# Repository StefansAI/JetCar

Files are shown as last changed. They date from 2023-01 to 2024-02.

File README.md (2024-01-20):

<h1 style="text-align: center;">JetCar</h1>
<h2 style="text-align: center;">The mini self-driving car project</h2>
<br>
<div style="text-align: center;">
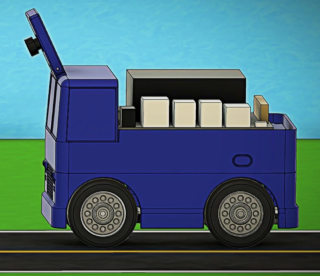
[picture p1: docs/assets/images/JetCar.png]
  
</div>
<br>
The JetCar project is based on ideas from <a href="https://github.com/NVIDIA-AI-IOT/jetbot">JetBot</a> and <a href="https://github.com/NVIDIA-AI-IOT/jetracer">JetRacer</a>. It utilizes the <a href="https://developer.nvidia.com/embedded/jetson-nano-developer-kit">Jetson Nano Developer Kit</a>, the OLED display and battery pack from JetBot and the steering servo control from JetRacer. But this project includes a completely new mechanical design, as compact as possible with these components. 
The goal is not speed or road following alone, but navigating on a street map autonomously, recognizing intersections and turning left or right on user request when the turn is allowed. To do this, JetCar has to recognize intersections and a few signs on the street.
<br>
<div style="text-align: center;">
  
</div>
<br>
The project is organized into following folders:
<br><br>

1. firmware
    - jetcar: Jupyter notebooks and python files to run in the JetCar
    - offline_debug: python files for offline debugging of firmware recordings
    - SD card install script 
<br><br>

2. mechanical
    - step_files: all step files of the car design
    - stl_files: all stl files for 3D printer
<br><br>

3. tools
    - bin: Windows executables
    - source: Full C# source code projects for the executables 
    - Jupyter notebook for training
<br><br>

To download just one sub folder from this repository, <a href="https://www.gitkraken.com/learn/git/github-download#how-to-download-a-folder-from-github">read here</a> or enter the URL directly in <a href="https://download-directory.github.io/"> https://download-directory.github.io/.</a> 
<br><br>
More documentation:<br>
- <a href="docs/BOM.md">BOM</a><br>
- <a href="docs/Assembly.md">Assembly</a><br>
- <a href="docs/SD%20Card%20Setup.md">SD Card Setup</a><br>
- <a href="docs/Data%20Preparation.md">Data Preparation with ImageSegmenter</a><br>
- <a href="docs/Model%20Training.md">Model Training</a><br>
- <a href="docs/StreetMaker.md">Street Maker</a><br>
- <a href="docs/Operation.md">Operation</a><br>
- <a href="docs/Debugging.md">Debugging</a><br>
<br><br>
Videos:<br>
- <a href="https://youtu.be/Dyagu1U4WaQ">JetCar Part 1 - Introduction</a><br>
- <a href="https://youtu.be/SRJtpAVrnXM">JetCar Part 2 – Assembly</a><br> 
- <a href="https://youtu.be/EU15R7dB3os">JetCar Part 3 - Firmware Setup</a><br>
- <a href="https://youtu.be/G4PKwO-Vvck">JetCar Part 4 - Data Preparation</a><br>
- <a href="https://youtu.be/1_ItpaHLQUw">JetCar Part 5 - Model Training</a><br>
- <a href="https://youtu.be/k-taHFnwKoY">JetCar Part 6 - StreetMaker</a><br>
- <a href="https://youtu.be/uBuOR0Mm2eY">JetCar Part 7 - Firmware</a><br>
- <a href="https://youtu.be/s89fhRwG_2A">JetCar Part 8 - Demonstration</a><br>
<br><br>

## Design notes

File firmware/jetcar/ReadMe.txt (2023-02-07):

Copy the contents of notebooks into the $HOME/JetCar/notebooks folder of the Jetson Nano via Jupyter.

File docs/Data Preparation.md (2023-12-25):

<h1 style="text-align: center;">JetCar</h1>
<h2 style="text-align: center;">Data Preparation with ImageSegmenter</h2>
<br><br>
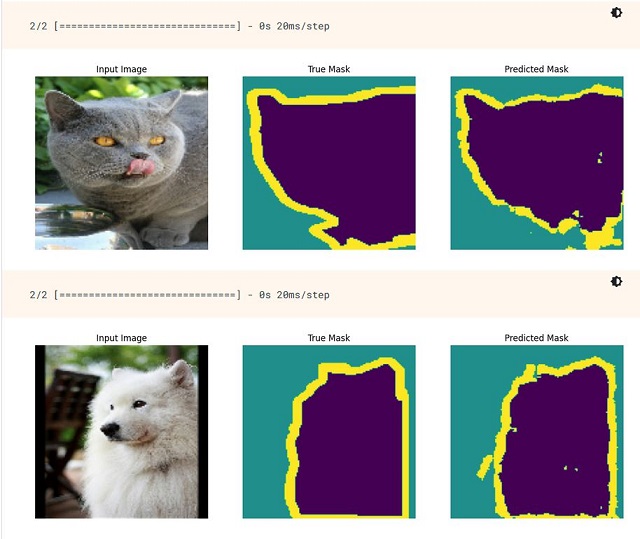
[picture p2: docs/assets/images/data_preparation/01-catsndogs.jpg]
<br><br>
Tensorflow.org has very nice <a href="https://www.tensorflow.org/tutorials/images/segmentation">tutorials to go through and even execute online.</a> One of them is about <a href="https://www.tensorflow.org/tutorials/images/segmentation">Image Segmentation</a> and the example is using a cats and dogs dataset. The model is trained on a mask to separate background from animal.
<br><br>
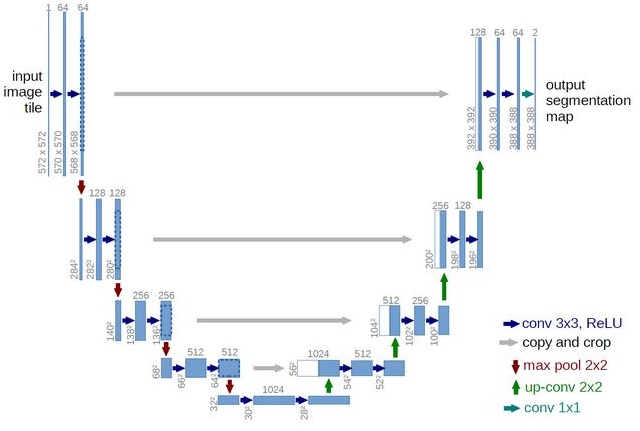
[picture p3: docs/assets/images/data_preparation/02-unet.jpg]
<br><br>
The <a href="https://lmb.informatik.uni-freiburg.de/people/ronneber/u-net/">U-Net</a> architecture contains a downsample path followed by an upsample path, abstracting features and resulting in a classification map. 
<br><br>
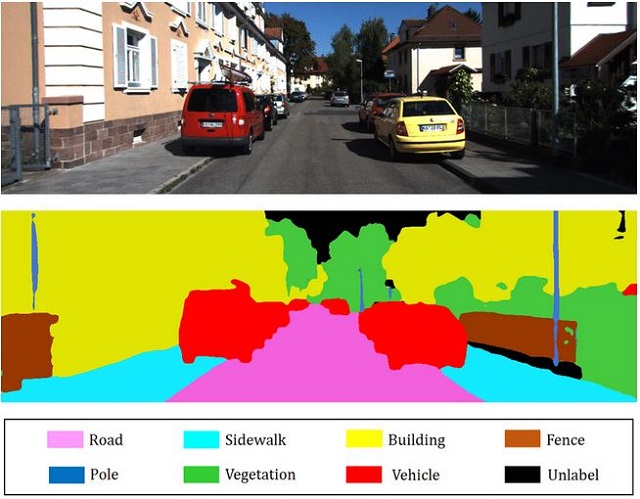
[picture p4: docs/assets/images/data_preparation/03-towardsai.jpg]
<br><br>
There are a lot of examples online. This one from the <a href="https://towardsai.net/p/l/machine-learning-7">TowardsAI Website</a> looks like something for this project.
<br><br>
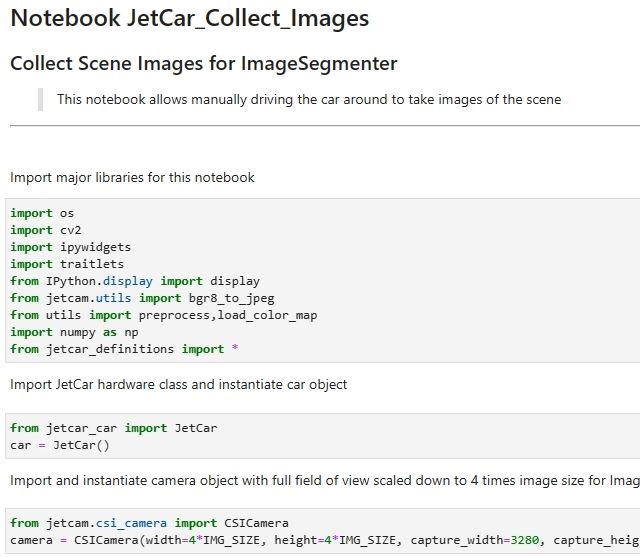
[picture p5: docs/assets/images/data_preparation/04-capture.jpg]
<br><br>
The <a href="https://github.com/NVIDIA-AI-IOT/jetbot">JetBot</a> project contained a Jupyter notebook to capture images of the scene for its own training (data_collection.ipynb). A similar version is part of the firmware notebooks for the JetCar (<a href="https://github.com/StefansAI/JetCar/tree/main/firmware/jetcar/notebooks/JetCar_Collect_Images.ipynb">JetCar_Collect_Images.ipynb</a>).<br>It allows manually driving the car around remotely and to hit a button to capture scene images. When done, the recorded images can be zipped and downloaded to the PC.<br>
JetBot and JetCar use image sizes of 224x224 for the inference. For better data augmentation however, the recorded images are here 4 times as big in both dimensions. 
<br><br>
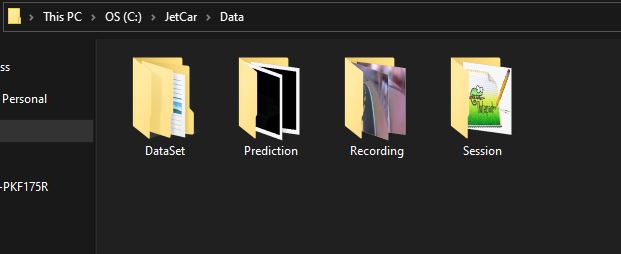
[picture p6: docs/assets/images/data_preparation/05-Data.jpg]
<br><br>
Now a tool was needed to create masks for each image. This tool happens to be now part of this repository as <a href="https://github.com/StefansAI/JetCar/tree/main/tools/bin/ImageSegmenter">compiled executable </a>and as <a href="https://github.com/StefansAI/JetCar/tree/main/tools/source/ImageSegmenter">full source code project.</a><br>
The Data folder for the ImageSegementer has to have a subfolder called "Recording", where all captured images need to go. 
<br><br>
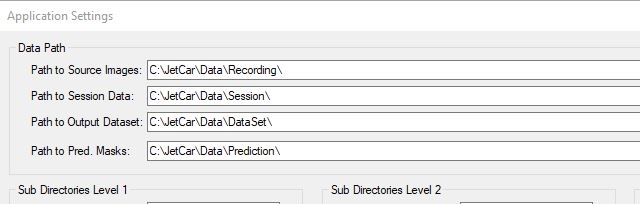
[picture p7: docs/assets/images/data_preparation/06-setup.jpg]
<br><br>
The very first time, this application is executed, it might prompt you to check and possibly correct the data path entries in the Settings dialog. A configuration file will be created to reload the last settings at startup.
<br><br>
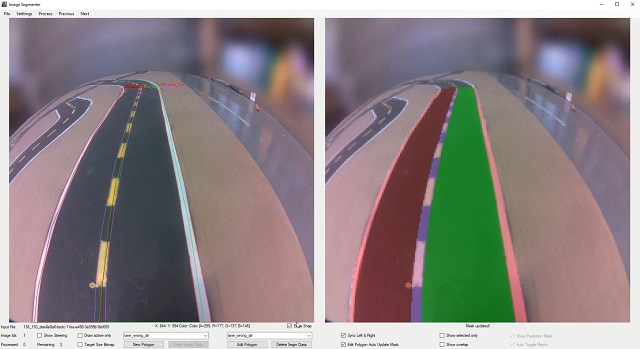
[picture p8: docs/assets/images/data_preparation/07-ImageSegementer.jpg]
<br><br>
The basic idea of this application is going through the recorded images one by one and creating the mask for each. The full resolution image is shown on the left side and the downsampled version as background on the right.
<br><br>
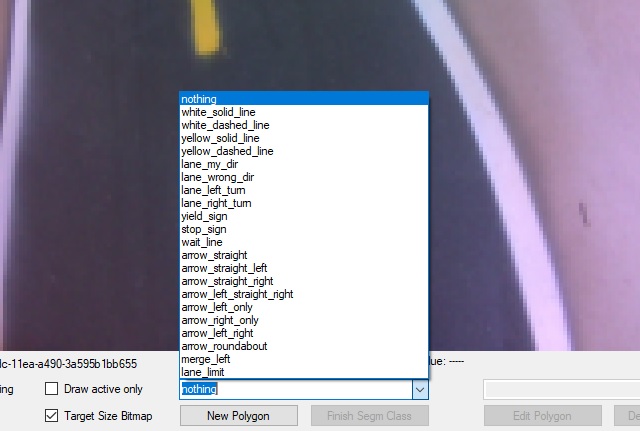
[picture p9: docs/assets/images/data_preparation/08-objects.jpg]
<br><br>
Every area to represent any specific class will have to be outlined with a polygon. To start outlining, select an object class from the combo box and hit "New Polygon". <br>Outline the area with the mouse and left click everywhere, where a polygon point needs to be added. When close to an edge, the point will be automatically snapped to the edge, but this function can be disabled with a check box. <br>A left double click closes the polygon and ends the mouse entry. Hit the "Finish Segm Class" button to finalize it. The polygon changes to the class color and the enclosed area appears in the same color transparent on top of the scene background on the right side.
<br><br>
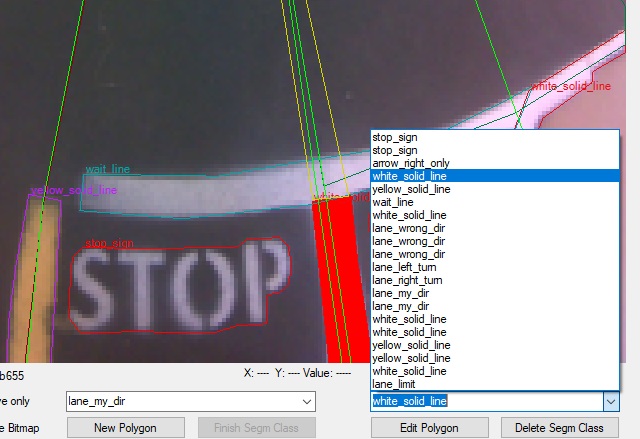
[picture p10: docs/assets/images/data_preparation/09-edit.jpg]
<br><br>
Every class polygon already entered will show up in the edit combobox. To identify the correct one out of several same classes, click on one and it will be highlighted as red filled polygon.
<br><br>
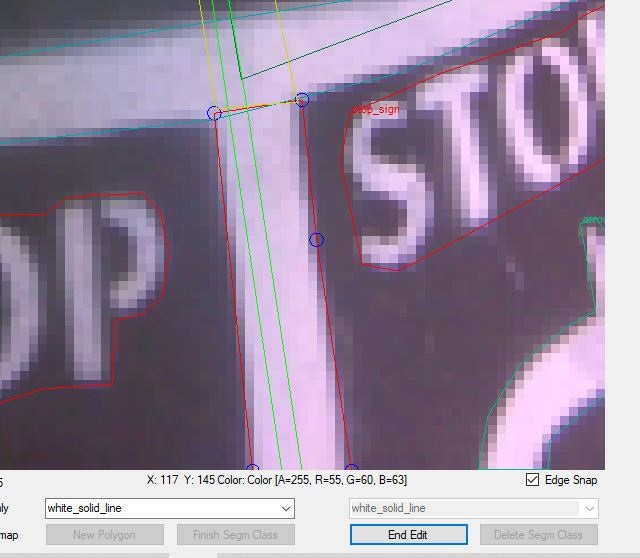
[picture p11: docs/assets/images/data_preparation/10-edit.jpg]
<br><br>
Hit the "Edit Polygon" to make changes. The polygon points are marked as circles and can be grabbed with the left mouse button and moved around until the left mouse button is released. <br>Scroll the mouse wheel to zoom in or out from the current position. <br>To add a point, left click on the polygon line and the drag newly created point in position. <br>To delete a point, just right click on it.<br>
The class selection box to the left shows the same class, but is accessible to change the assignment.<br>
Hit the "End Edit" Button to finalize the changes made.
<br><br>
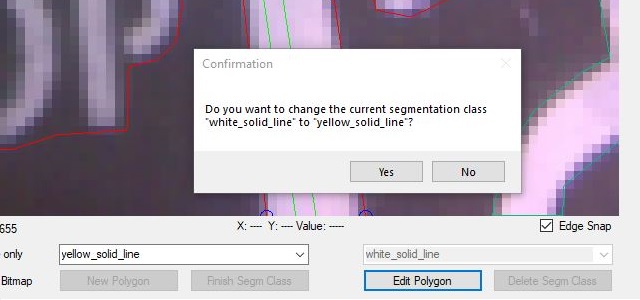
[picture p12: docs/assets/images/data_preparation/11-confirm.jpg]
<br><br>
In case, the class change was not intended, a confirmation dialog comes up. "No" will go back to edit mode. 
<br><br>
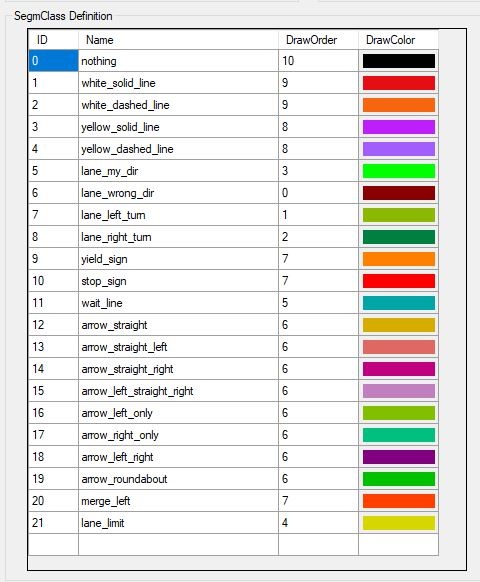
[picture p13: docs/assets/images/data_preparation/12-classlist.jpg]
<br><br>
The list of class definitions can be freely changed in the settings dialog and this application can be used for completely different types of segmentation tasks.
The ID is the code to represent this class in the mask, the name can be anything and the draw order controls handling of polygon overlaps. When a mask is generated, the application starts with all objects with DrawOrder=0, then 1 etc. This guarantees that for instance the lanes will be drawn in an order on top of eachother, then arrows and texts and lines at last. Knowing the draw order helps outlining with overlap.
<br><br>
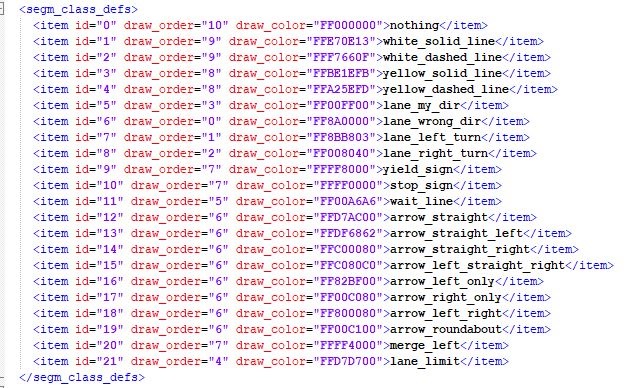
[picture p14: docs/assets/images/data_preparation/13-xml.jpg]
<br><br>
Together with all other settings, the class definitions are stored in the settings XML file and can be also overwritten there with a text editor when necessary.<br>
Attention: Keep the file structure intact or things will go south!
<br><br>
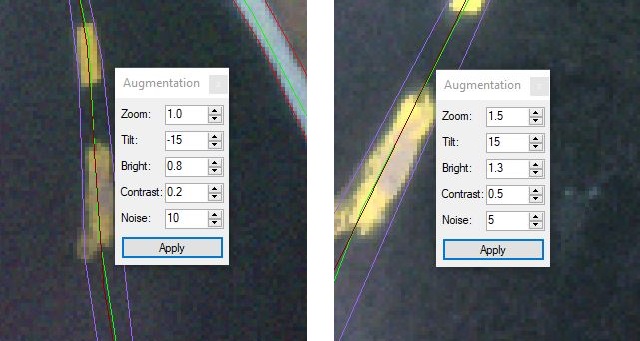
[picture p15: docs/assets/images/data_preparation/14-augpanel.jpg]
<br><br>
Under the "Process" menu, the Augmentation panel can be opened. It allows testing the available augmentation parameter on the current image. Read here for more info on <a href="https://www.tensorflow.org/tutorials/images/data_augmentation">Data Augmentation</a><br>
The example image above demonstrates two different sets of these parameters on the same image detail. It is good to test some parameter before creating a dataset with parameters, that don't work well together.
<br><br>
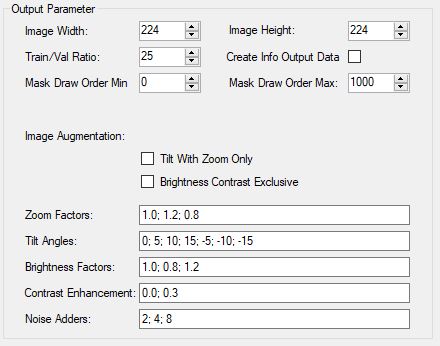
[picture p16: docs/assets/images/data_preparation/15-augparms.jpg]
<br><br>
In the Settings dialog, there is a list of augmentation parameter to go through when creating a dataset. The numbers have to be separated with ";". Any sequence of numbers can be entered. <br>
But keep in mind all variations multiply the number of dataset images. In the screen shot example, one recorded image will result in 3x7x3x2x3=378 image/mask sets. In other words, 100 original images end up as 37800 sets. Checking the 2 checkboxes reduces the multiplier by excluding some of the combinations.<br>
The "Train/Val Ratio" parameter above defines the ratio between the 2 output folders for training and validation. 25 for instance means, about every 25th set goes into the validation folder.
<br><br>
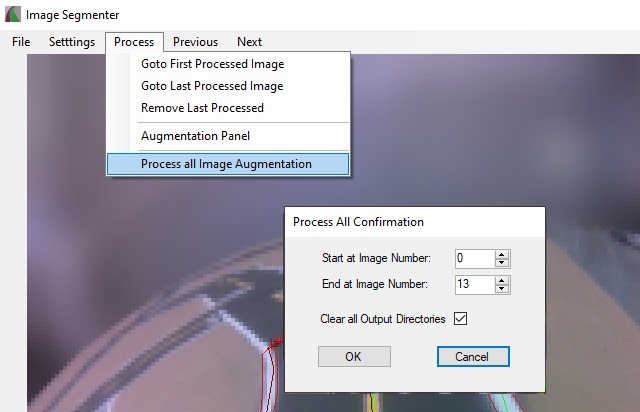
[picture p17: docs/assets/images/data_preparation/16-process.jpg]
<br><br>
After all recorded images have gone through the class outlining process, the dataset can be generated via the "Process" menu. After the confirmation, the dataset generation starts and can be observed while running for some longer time.<br>
In the end, all images and masks are in the DataSet folder sorted into subfolders for images and masks and their subfolders for training and validation.<br>
All mask files are stored into PNG files that appear black, since the class codes are counting from 0 up.<br>
The DataSet folder can be zipped up into JetCar_DataSet.zip for a model training run.
<br><br><br>

- <a href="Model%20Training.md">Model Training</a><br>
- <a href="StreetMaker.md">Street Maker</a><br>
- <a href="Operation.md">Operation</a><br>

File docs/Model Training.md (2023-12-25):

<h1 style="text-align: center;">JetCar</h1>
<h2 style="text-align: center;">Data Preparation with ImageSegmenter</h2>
<br><br>
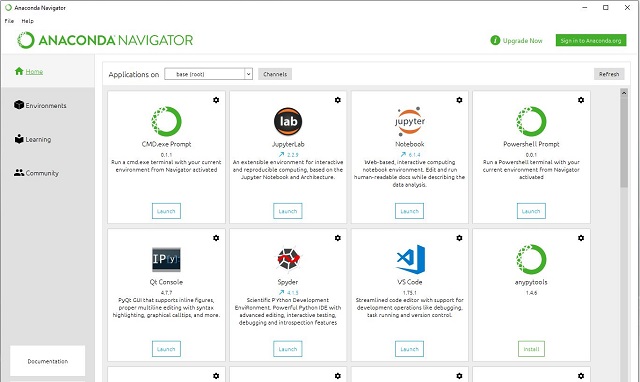
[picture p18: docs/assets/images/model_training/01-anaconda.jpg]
<br><br>
The training can be performed on the PC after installing <a href="https://docs.anaconda.com/anaconda/install/windows/">Anaconda</a> and then Jupyter notebook and many other tools and libraries. But training with thousands of images can easily take days and turn the PC into a heater. So, moving into the cloud removes the stress from the local machine.
<br><br>
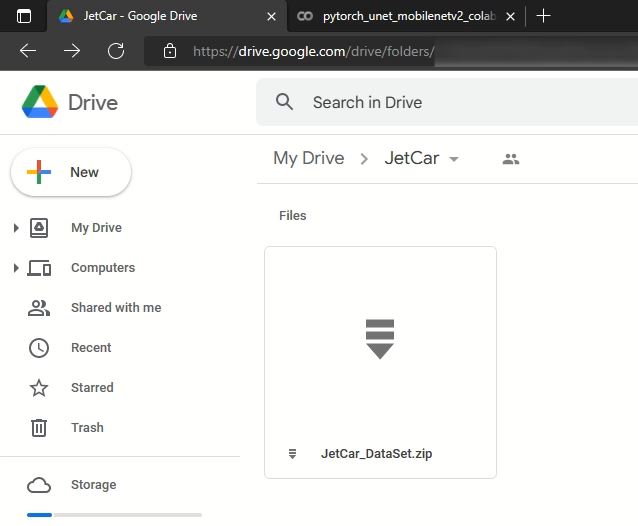
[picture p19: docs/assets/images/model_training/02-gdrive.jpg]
<br><br>
The first step is getting a Google drive account and copy the dataset zip file there.
<br><br>
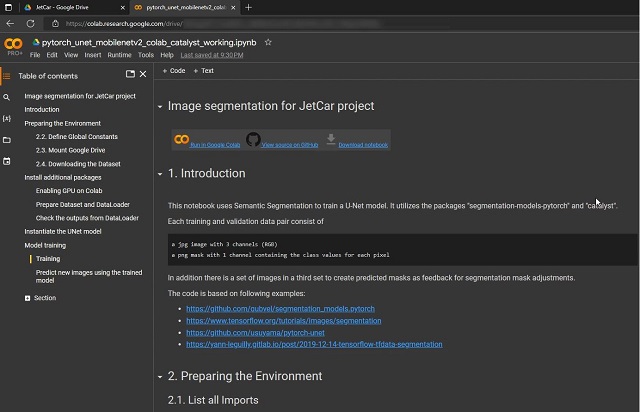
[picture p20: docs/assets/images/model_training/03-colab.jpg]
<br><br>
Then open the <a href="https://github.com/StefansAI/JetCar/tree/main/tools/jetcar_pytorch_unet_mobilenetv2_catalyst.ipynb">training notebook</a> in <a href="https://colab.research.google.com/">Google Colab</a>. For faster execution and stable connections upgrade to Colab Pro or Colab Pro+ to purchase units. Make sure to change runtime type to GPU and High-RAM using A100.
<br><br>
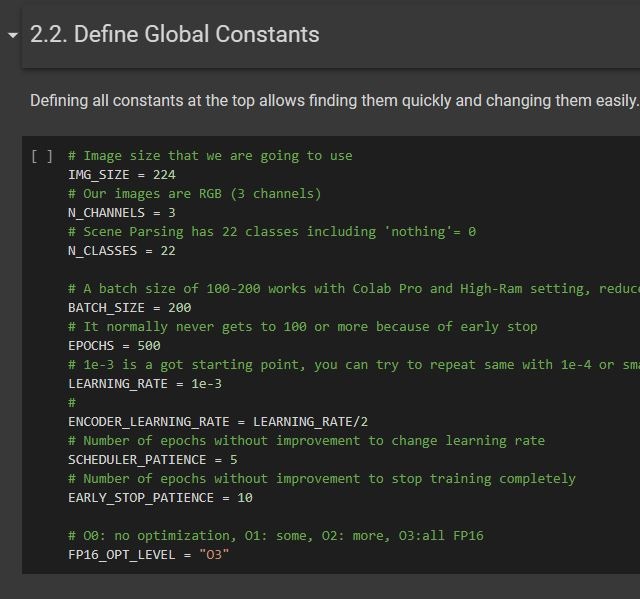
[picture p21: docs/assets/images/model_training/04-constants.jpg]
<br><br>
The notebook starts with defining a couple of constants. The ImageSegmenter defined 22 classes, so N_CLASSES should be 22.<br>
The batch size will have to be reduced drastically on a PC and maybe on the standard Colab version.<br>
Everything else can be left as is. However, when a training run is stopped because of disconnection or any other cause, it can be restarted with the last learning rate of the of the disconnected run before. The notebook will pick up the last saved model weights file from the Google drive.
<br><br>
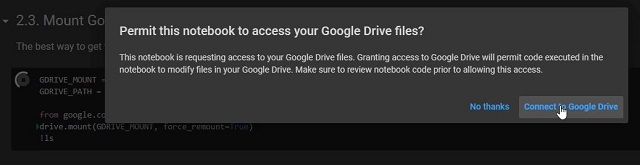
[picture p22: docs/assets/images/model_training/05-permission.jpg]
<br><br>
Now hit "Run all" from the "Runtime" menu. After a moment, the notebook tries to connect to the Google drive and asks for permission.
<br><br>
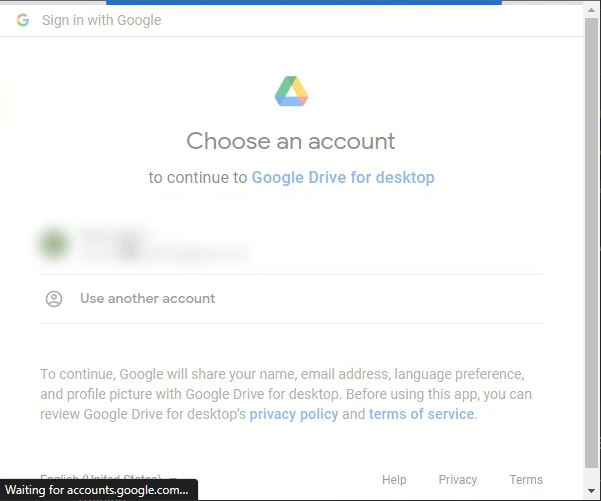
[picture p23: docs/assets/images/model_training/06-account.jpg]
<br><br>
If the Google drive is open in the same browser, the dialog will offer to connect to it. Click on the account (here blurred).
<br><br>
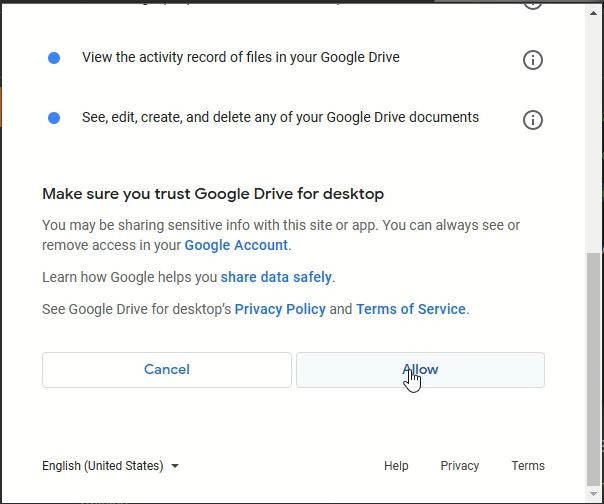
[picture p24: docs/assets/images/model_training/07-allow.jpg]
<br><br>
Then scroll down and hit allow.
<br><br>
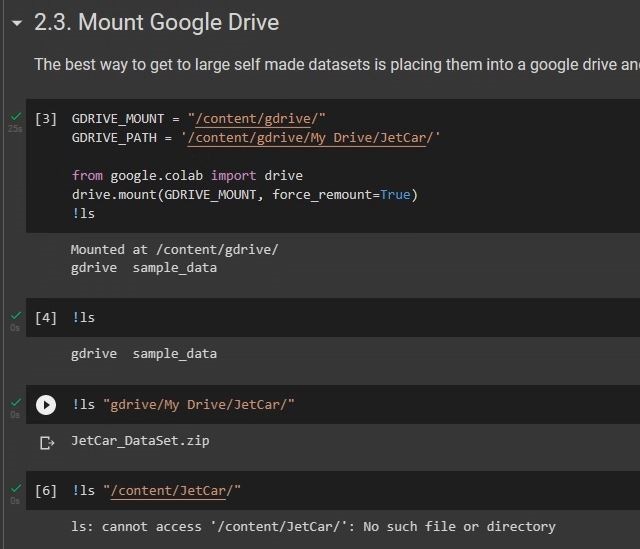
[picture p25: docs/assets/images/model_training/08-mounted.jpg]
<br><br>
The google drive will be mounted to the Colab machine, ready to download data.<br>
The ls commands show the contents of the Google drive and the cloud machine. The JetCar folder does not exist yet on the Colab machine.
<br><br>
<br><br>
Downloading the dataset file and unzipping takes a while, depending on the size. When done, the notebook lists the number of images for training, validation and prediction.
<br><br>
<br><br>
The notebook will install a number of additional libraries, including Catalyst.<br>
Scrolling down to the cell, where the training is running, log entries will start showing up for each epoch. Each runs a few minutes. After the SCHEDULER_PATIENCE number of epochs without improvement, the learning rate will decrease.<br>
Whenever the message comes up, that it saves the model weights, the file is copied to the Google drive, so the progress is not lost at a disconnection.
<br><br>
<br><br>
After few epochs, the TensorBoard some cells above will start showing the results in different graphs after setting to scalars and reload.
<br><br>
<br><br>
When the training is done after no improvements, the notebook continues.
<br><br>
<br><br>
All prediction test images are now run through model inference to create the prediction masks, which are then zipped up and stored in the Google drive.
<br><br>
<br><br>
The training will finish when despite reducing the learning rate no further improvement was achieved for EARLY_STOP_PATIENCE number of epochs. The notebook will then continue with the next cells and run the prediction. The prediction results are copied over to the Google drive and are now available for download to the local PC.
<br><br>
<br><br>
Extract the prediction masks into the prediction subfolder of the ImageSegmenter Data path.
<br><br>
<br><br>
When starting the ImageSegmenter application now, it will toggle the prediction mask on the right side with the true mask for each image. Here is the prediction mask and below the true mask.
<br><br>
<br><br>
True mask to compare with predicted mask above.
<br><br><br>

- <a href="Data%20Preparation.md">Data Preparation with ImageSegmenter</a><br>
- <a href="StreetMaker.md">Street Maker</a><br>
- <a href="Operation.md">Operation</a><br>

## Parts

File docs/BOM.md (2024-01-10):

<h1>Bill of Materials</h1>
<br>
<h3>Needed parts</h3>
<table>
<thead>
<tr>
<th><strong>Part</strong></th>
<th align="right"><strong>Quantity</strong></th>
<th align="right"><strong>Cost</strong></th>
<th><strong>URL</strong></th>
<th><strong>Notes</strong></th>
</tr>
</thead>
<tbody>
<tr>
<td>Jetson Nano</td>
<td align="right">1</td>
<td align="right">$149.00</td>
<td><a href="https://developer.nvidia.com/embedded/buy/jetson-nano-devkit">NVIDIA</a>,<a href="https://www.arrow.com/en/products/945-13450-0000-100/nvidia">Arrow</a></td>
<td></td>
</tr>
<tr>
<td>Cooling Fan</td>
<td align="right">1</td>
<td align="right">$8.32</td>
<td><a href="https://www.amazon.com/gp/product/B07TD2PCM5/ref=ppx_yo_dt_b_asin_title_o04_s02?ie=UTF8&psc=1">Amazon</a></td>
<td></td>
</tr>
<tr>
<td>Wifi Card</td>
<td align="right">1</td>
<td align="right">$22.00</td>
<td><a href="https://www.amazon.com/gp/product/B01MZA1AB2/ref=ppx_yo_dt_b_asin_title_o03_s04?ie=UTF8&psc=1">Amazon</a></td>
<td></td>
</tr>
<tr>
<td>Wi-Fi Antennas</td>
<td align="right">2</td>
<td align="right">$1.84</td>
<td><a href="https://www.arrow.com/en/products/2042811100/molex">Arrow</a></td>
<td></td>
</tr>
<tr>
<td>Micro SD card</td>
<td align="right">1</td>
<td align="right">$10.88</td>
<td><a href="https://www.amazon.com/SanDisk-Extreme-microSDXC-Memory-Adapter/dp/B09X7C7LL1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">Amazon</a></td>
<td>64GB</td>
</tr>
<tr>
<td>USB -> Barrel Cable</td>
<td align="right">1</td>
<td align="right">$7.00</td>
<td><a href="https://www.amazon.com/gp/product/B075112RM6/">Amazon</a></td>
<td>USB A -> 2.1mm Barrel Cable</td>
</tr>
<tr>
<td>Right angle USB cable</td>
<td align="right">1</td>
<td align="right">$8.99</td>
<td><a href="https://www.amazon.com/gp/product/B01N337FQF/ref=ppx_yo_dt_b_asin_title_o04_s00?ie=UTF8&psc=1">Amazon</a></td>
<td></td>
</tr>
<tr>
<td>Battery</td>
<td align="right">1</td>
<td align="right">$15.99</td>
<td><a href="https://amzn.to/2WRcIUe">Amazon</a></td>
<td>2x 5V/3A output, 10,000mAh, 130x68x15mm (5.1x2.6x0.59")</td>
</tr>
<tr>
<td><em>PiOLED</em> display</td>
<td align="right">1</td>
<td align="right">$13.23</td>
<td><a href="http://adafru.it/3527">Adafruit</a>, <a href="https://amzn.to/2GgxUxX">Amazon</a></td>
<td></td>
</tr>
<tr>
<td><em>PiOLED</em> header</td>
<td align="right">1</td>
<td align="right">$5.95</td>
<td><a href="http://adafru.it/1541">Adafruit</a>, <a href="https://amzn.to/2taLSJf">Amazon</a>, <a href="https://www.sparkfun.com/products/12792">Sparkfun</a></td>
<td>2x(3+) right angle male</td>
</tr>
<tr>
<td>Servo Motor Driver</td>
<td align="right">1</td>
<td align="right">$9.49</td>
<td><a href="https://www.amazon.com/gp/product/B01D1D0CX2/ref=ppx_yo_dt_b_asin_title_o04_s01?ie=UTF8&psc=1">Amazon</a><td>PCA9685 16 Channel 12-Bit PWM</td>
</tr>
<tr>
<td>Geared DC Motor</td>
<td align="right">2</td>
<td align="right">$10.68</td>
<td><a href="https://www.amazon.com/dp/B09GKXDTQD?psc=1&ref=ppx_yo2ov_dt_b_product_details">Amazon-10RPM<a>,<a href="https://www.amazon.com/gp/product/B07FYBQ7Z4/ref=ppx_yo_dt_b_asin_title_o05_s00?ie=UTF8&psc=1">Amazon-30RPM</a></td>
<td>6V between 10 and max 30RPM</td>
</tr>
<tr>
<td>Motor Driver H-Bridge</td>
<td align="right">1</td>
<td align="right">$7.99</td>
<td><a href="https://www.amazon.com/gp/product/B07S4FVY9M/ref=ppx_yo_dt_b_asin_title_o00_s01?ie=UTF8&psc=1">Amazon</a></td>
<td>1 Package contains 5 boards, need 2</td>
</tr>
<tr>
<td>Camera</td>
<td align="right">1</td>
<td align="right">$29.00</td>
<td><a href="https://www.mouser.com/ProductDetail/Leopard-Imaging/LI-IMX219-MIPI-FF-NANO-H145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">Mouser</a>,
<a href="https://www.amazon.com/gp/product/B07T43K7LC/ref=ppx_yo_dt_b_asin_title_o03_s00?ie=UTF8&psc=1">Amazon</a></td>
<td>LI-IMX219-MIPI-FF-NANO-<strong>H145</strong></td>
</tr>
<tr>
<td>Servo</td>
<td align="right">1</td>
<td align="right">$9.99</td>
<td><a href="https://www.amazon.com/TISEKER-Pieces-Compatible-Helicopter-Arduino/dp/B0BGPHD7MX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">Amazon</a></td>
<td>Any 9g - 14g metal gear, 90 degrees</td>
</tr>
<tr>
<td>Wheels</td>
<td align="right">2</td>
<td align="right">$8.95</td>
<td><a href="https://www.pololu.com/product/1090">Polulu</a></td>
<td>Need 2 Pairs (comes in pairs)</td>
</tr>
<tr>
<td>Philips Tapping Screws</td>
<td align="right">1</td>
<td align="right">$16.59</td>
<td><a href="https://www.amazon.com/gp/product/B075GC465B/ref=ppx_yo_dt_b_asin_title_o00_s00?ie=UTF8&psc=1">Amazon</a></td>
<td>For housing assembly, or similar 2mm</td>
</tr>
<tr>
<td>Hex Socket Tapping Screws</td>
<td align="right">1</td>
<td align="right">$9.99</td>
<td><a href="https://www.amazon.com/gp/product/B00YBMRAH4/ref=ppx_yo_dt_b_asin_title_o03_s03?ie=UTF8&psc=1">Amazon</a></td>
<td>For camera mount, or similar 2x M2</td>
</tr>
<tr>
<td>Hex Socket Screw Assortment Kit</td>
<td align="right">1</td>
<td align="right">$18.99</td>
<td><a href="https://www.amazon.com/gp/product/B06XKMNH4T/ref=ppx_yo_dt_b_asin_title_o01_s02?ie=UTF8&psc=1">Amazon</a></td>
<td>For front wheels, or any 2x M3 screws</td>
</tr>
<tr>
<td>Jumper wires</td>
<td align="right">1</td>
<td align="right">$5.45</td>
<td><a href="https://www.amazon.com/gp/product/B077NH83CJ/ref=ppx_yo_dt_b_asin_title_o03_s00?ie=UTF8&psc=1">Amazon</a></td>
<td></td>
</tr>
</tbody>
</table>
<br>
<h3>LED setup</h3>
<table>
<thead>
<tr>
<th><strong>Part</strong></th>
<th align="right"><strong>Quantity</strong></th>
<th align="right"><strong>Cost</strong></th>
<th><strong>URL</strong></th>
<th><strong>Notes</strong></th>
</tr>
</thead>
<tbody>
<tr>
<td>LED white</td>
<td align="right">4</td>
<td align="right">$0.29</td>
<td><a href="https://www.digikey.com/en/products/detail/tt-electronics-optek-technology/OVLEW1CB9/827113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">Digikey</a></td>
<td>5mm diameter for head lights</td>
</tr>
<tr>
<td>Resistor</td>
<td align="right">4</td>
<td align="right">$0.10</td>
<td><a href="https://www.digikey.com/en/products/detail/stackpole-electronics-inc/CF18JT91R0/1741788">Digikey</a></td>
<td>90..120Ohm serial resistors for headlights.</td>
</tr>

<td>LED red</td>
<td align="right">4</td>
<td align="right">$0.42</td>
<td><a href="https://www.digikey.com/en/products/detail/lumex-opto-components-inc/SSL-LX2573ID/270845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">Digikey</a></td>
<td>2x5mm rectangular for tail light and brake lights</td>
</tr>
<td>LED amber</td>
<td align="right">4</td>
<td align="right">$0.42</td>
<td><a href="https://www.digikey.com/en/products/detail/lumex-opto-components-inc/SSL-LX2573AD/270843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">Digikey</a></td>
<td>2x5mm rectangular for turn signals</td>
</tr>
<td>LED wires</td>
<td align="right">1</td>
<td align="right">$5.45</td>
<td><a href="https://www.amazon.com/gp/product/B077NH83CJ/ref=ppx_yo_dt_b_asin_title_o03_s00?ie=UTF8&psc=1">Amazon</a></td>
<td>Or other similar wires.</td>
</tr>
</tbody>
</table>
<br>
<h3>Nice to have</h3>
<table>
<thead>
<tr>
<th><strong>Part</strong></th>
<th align="right"><strong>Quantity</strong></th>
<th align="right"><strong>Cost</strong></th>
<th><strong>URL</strong></th>
<th><strong>Notes</strong></th>
</tr>
</thead>
<tbody>
<tr>
<td>Power supply</td>
<td align="right">1</td>
<td align="right">$7.50</td>
<td><a href="http://bit.ly/af1995">Adafruit</a></td>
<td>Micro USB, 5V, 2.5A</td>
</tr>
<tr>
<td>Matte Printer Paper</td>
<td align="right">1</td>
<td align="right">$29.99</td>
<td><a href="https://www.amazon.com/gp/product/B0B3QWXVZC/ref=ppx_yo_dt_b_asin_image_o01_s00?ie=UTF8&th=1">Amazon</a></td>
<td>Or similar thick matte paper</td>
</tr>

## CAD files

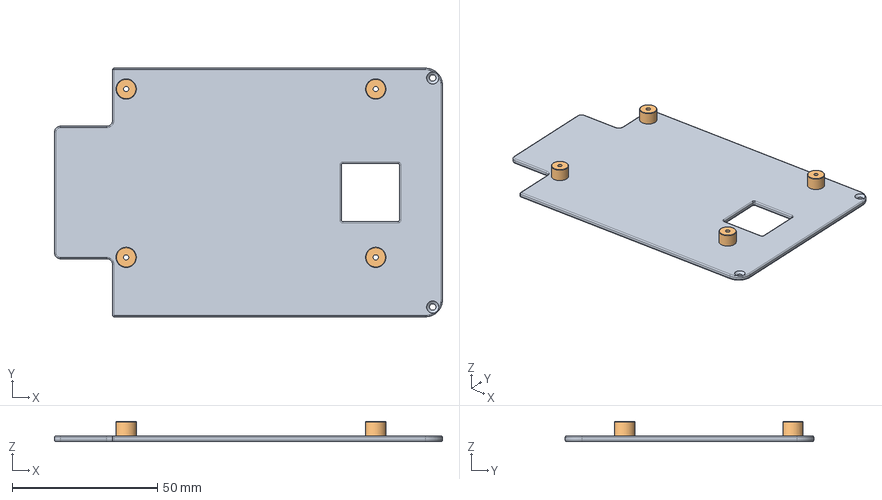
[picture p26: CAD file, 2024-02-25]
mechanical/step_files/Flatbed-JetsonNano.step
133.7 x 85.7 x 7.00 mm

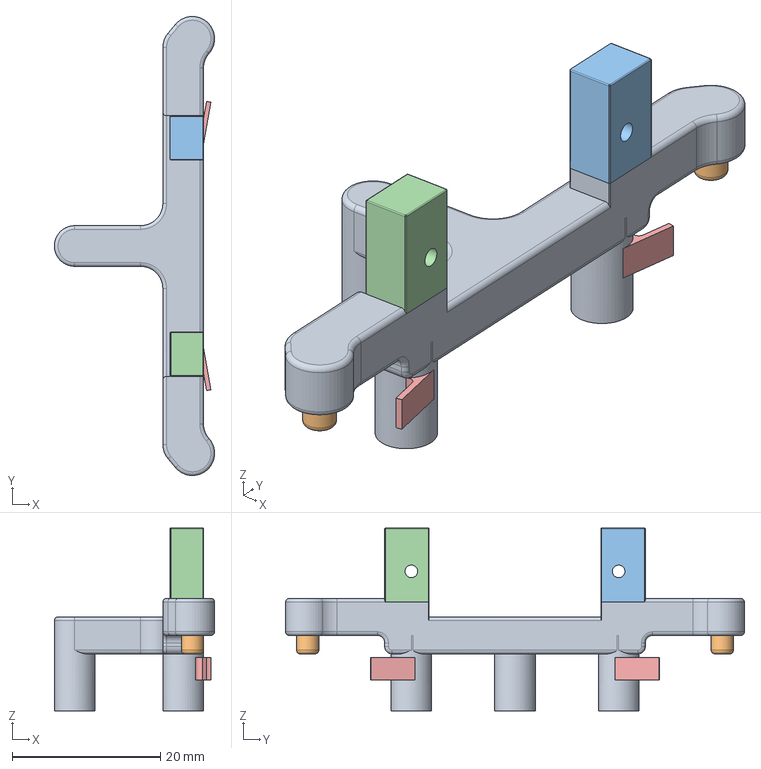
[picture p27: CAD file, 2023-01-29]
mechanical/step_files/Front Axle.step
21.6 x 62.0 x 24.7 mm

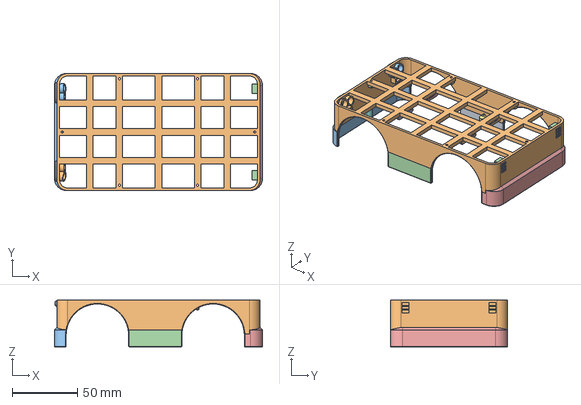
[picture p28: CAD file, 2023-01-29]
mechanical/step_files/LowerBody.step
160.0 x 90.0 x 36.0 mm

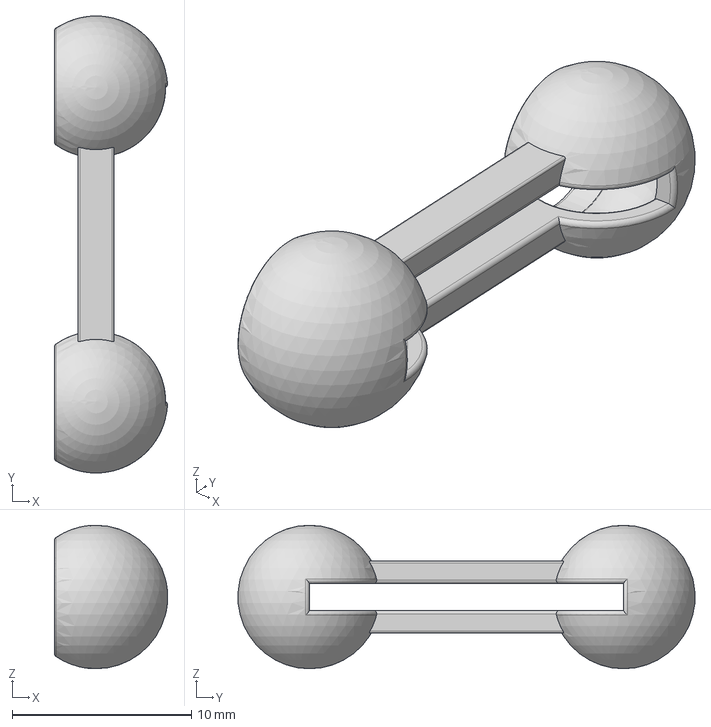
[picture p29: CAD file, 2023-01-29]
mechanical/step_files/Pushrod.step
6.32 x 25.5 x 8.00 mm

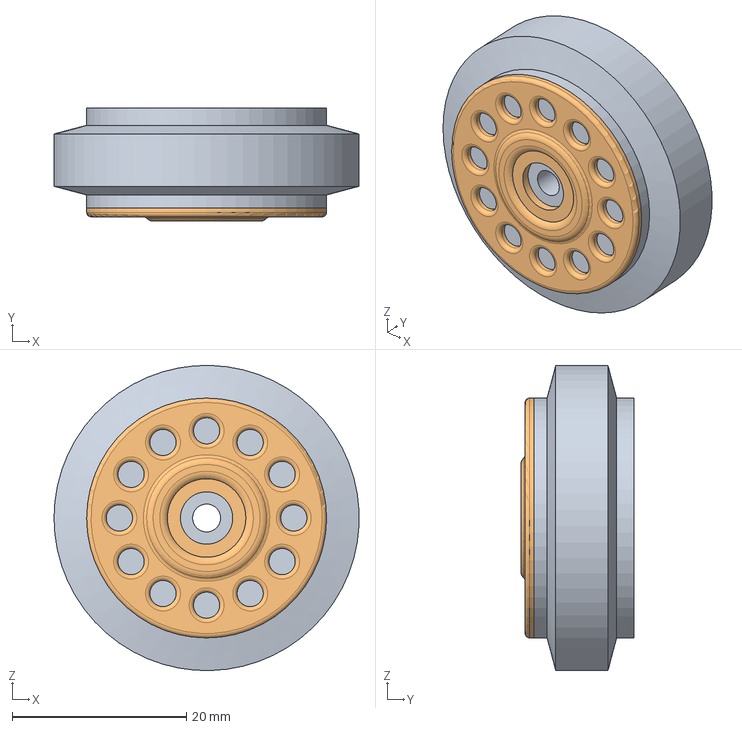
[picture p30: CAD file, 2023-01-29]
mechanical/step_files/Wheel Spindle.step
35.0 x 13.0 x 35.0 mm

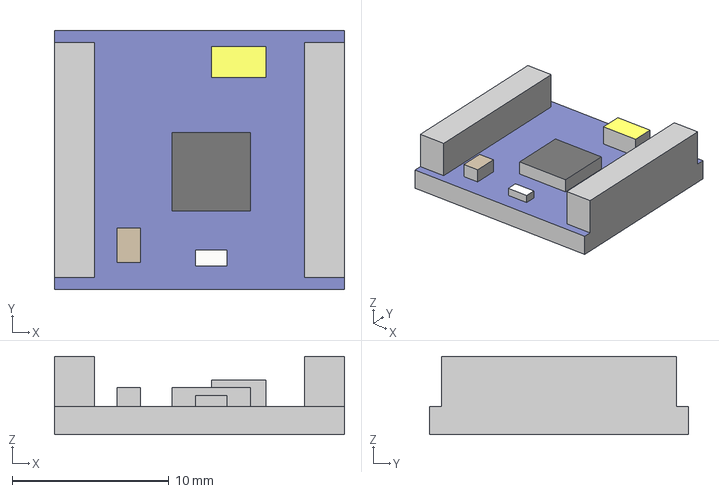
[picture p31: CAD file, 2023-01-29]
mechanical/step_files/H-Bridge.step
18.5 x 16.5 x 5.00 mm

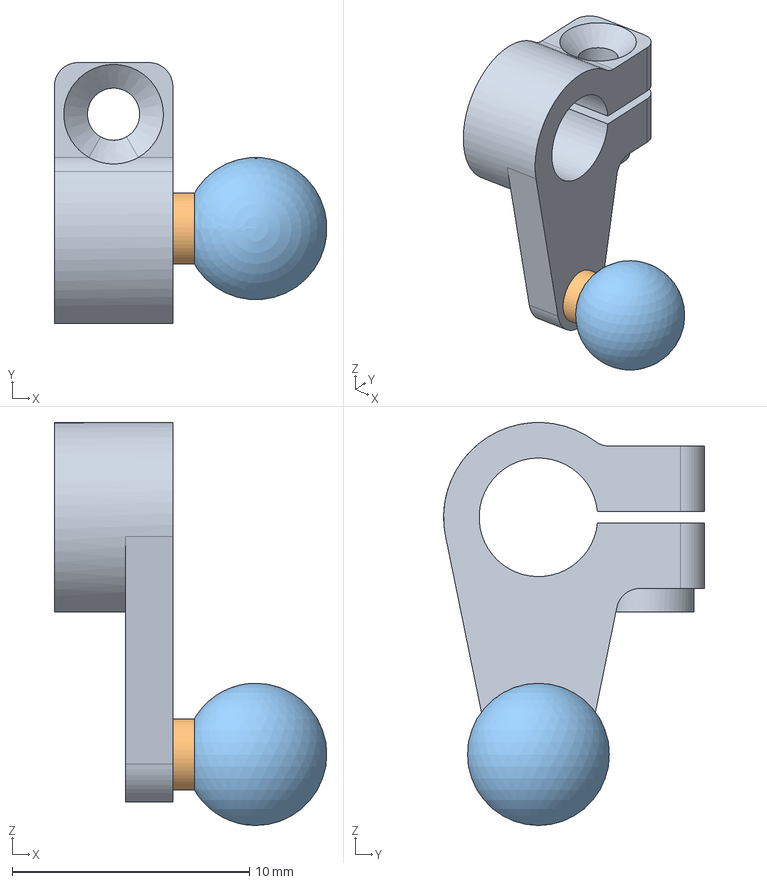
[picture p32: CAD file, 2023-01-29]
mechanical/step_files/Servo Arm.step
11.5 x 11.0 x 17.0 mm

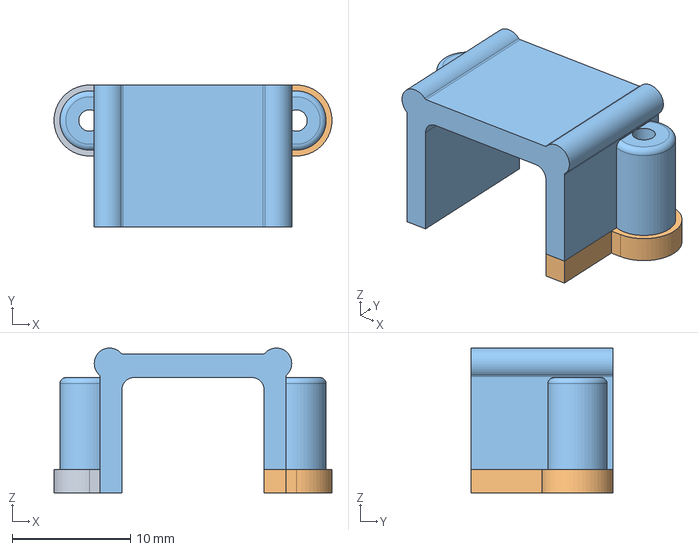
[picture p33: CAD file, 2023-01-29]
mechanical/step_files/MotorBracket.step
23.5 x 12.0 x 12.2 mm

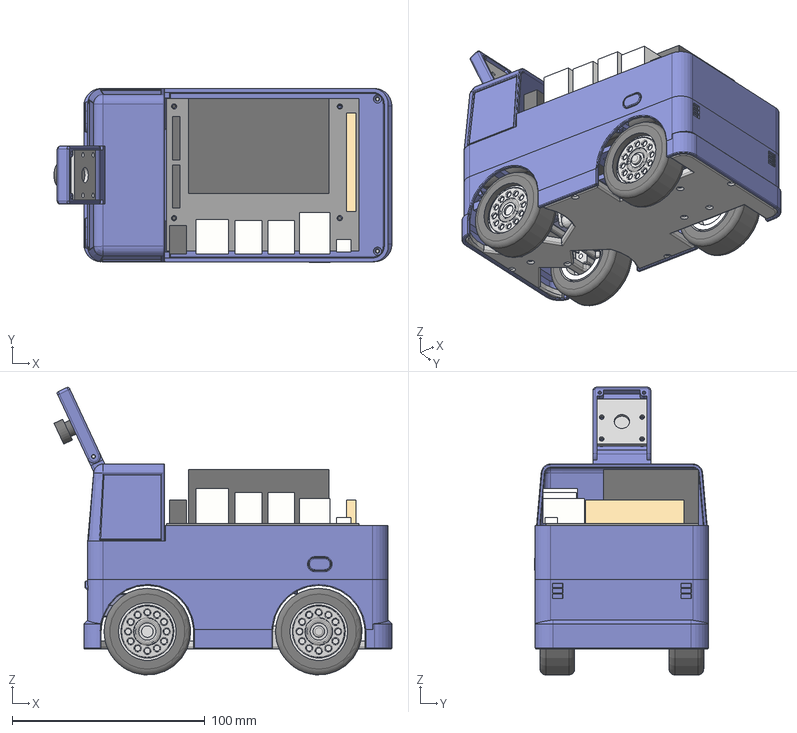
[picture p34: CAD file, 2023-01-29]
mechanical/step_files/JetCar.step
175.5 x 90.4 x 149.3 mm
Wheels
Undercarriage
Wheel Spindle
Steering Rack
Rim
Servo
Servo Controller
Battery
Jetson Nano
Servo Arm
HubCap
Front Axle
LowerBody
UpperBody
Camera Mount Top
Flatbed
MotorBracket x 2
H-Bridge x 2
OnOffSwitch
ChargerLid
Camera
Pushrod

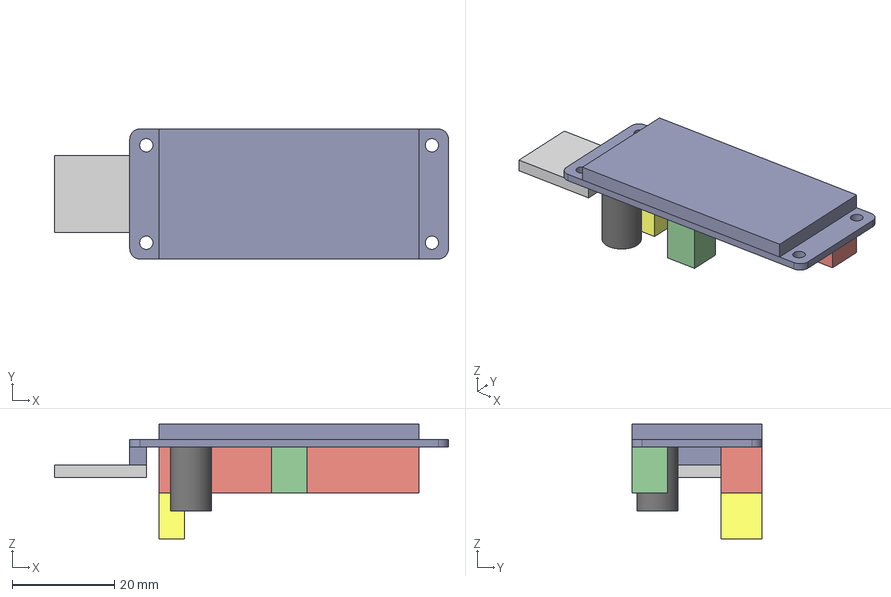
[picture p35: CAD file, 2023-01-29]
mechanical/step_files/Servo Controller.step
77.2 x 25.5 x 22.5 mm

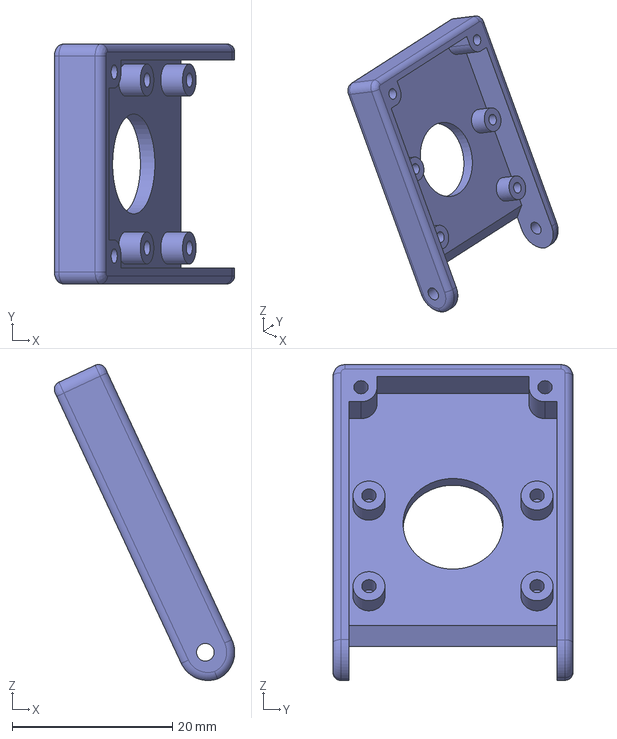
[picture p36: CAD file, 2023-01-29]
mechanical/step_files/Camera Mount Top.step
22.6 x 30.0 x 39.5 mm

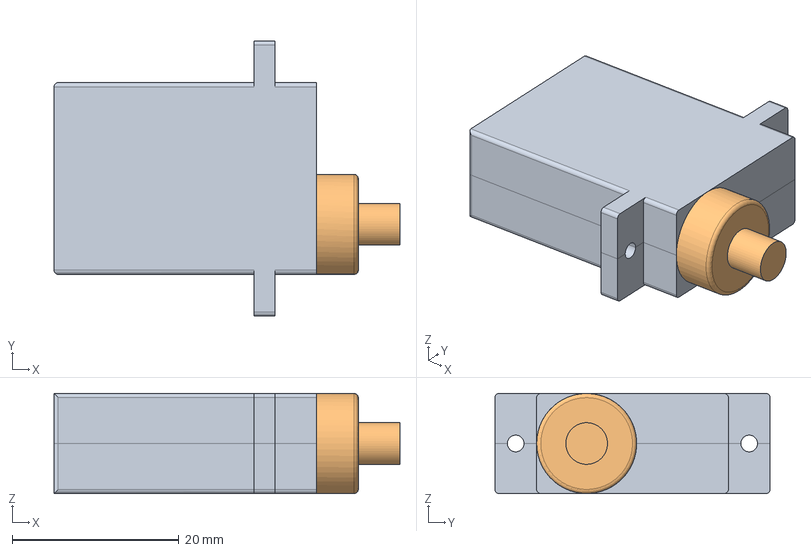
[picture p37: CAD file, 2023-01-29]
mechanical/step_files/Servo.step
41.5 x 33.0 x 12.0 mm

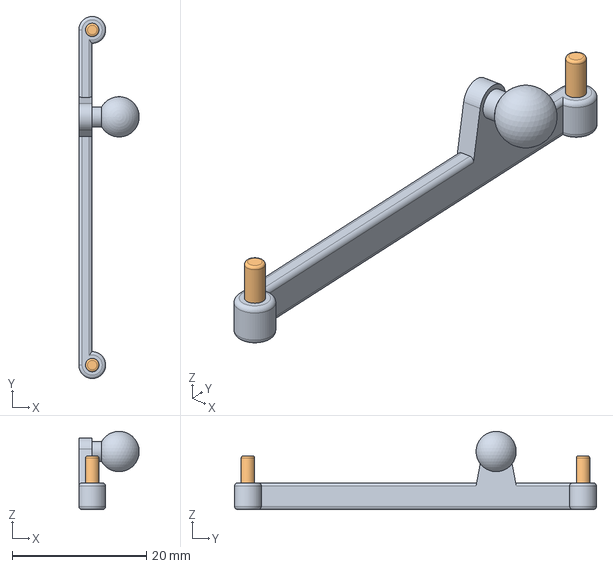
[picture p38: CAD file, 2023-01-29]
mechanical/step_files/Steering Rack.step
8.99 x 53.9 x 11.7 mm

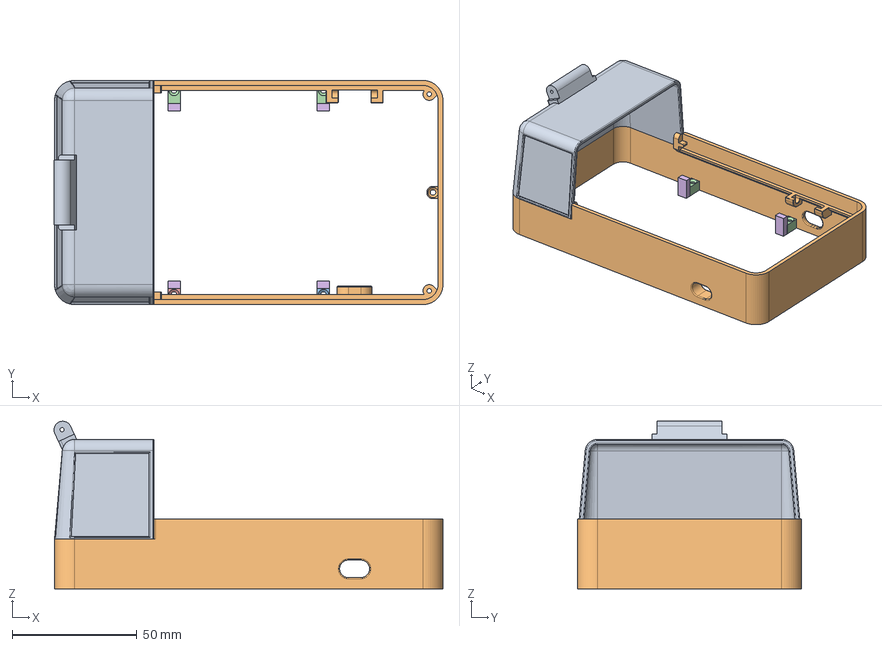
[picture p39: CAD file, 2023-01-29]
mechanical/step_files/UpperBody.step
156.2 x 90.0 x 67.3 mm

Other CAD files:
mechanical/step_files/Camera.step
mechanical/step_files/Undercarriage.step
mechanical/step_files/OnOffSwitch.step
mechanical/step_files/Jetson Nano.step
mechanical/step_files/Battery.step
mechanical/step_files/ChargerLid.step
mechanical/step_files/HubCap.step
mechanical/step_files/Rim.step
mechanical/stl_files/Camera Mount Top.stl
mechanical/stl_files/ChargerLid.stl
mechanical/stl_files/Flatbed-JetsonNano.stl
mechanical/stl_files/Front Axle.stl
mechanical/stl_files/HubCap.stl
mechanical/stl_files/MotorBracket.stl
mechanical/stl_files/OnOffSwitch.stl
mechanical/stl_files/Pushrod.stl
mechanical/stl_files/Rim.stl
mechanical/stl_files/Servo Arm.stl
mechanical/stl_files/Steering Rack.stl
mechanical/stl_files/Undercarriage.stl
mechanical/stl_files/UpperBody.stl
mechanical/stl_files/Wheel Spindle.stl

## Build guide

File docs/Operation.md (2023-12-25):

<h1 style="text-align: center;">JetCar</h1>
<h2 style="text-align: center;">Operation</h2>
<br>
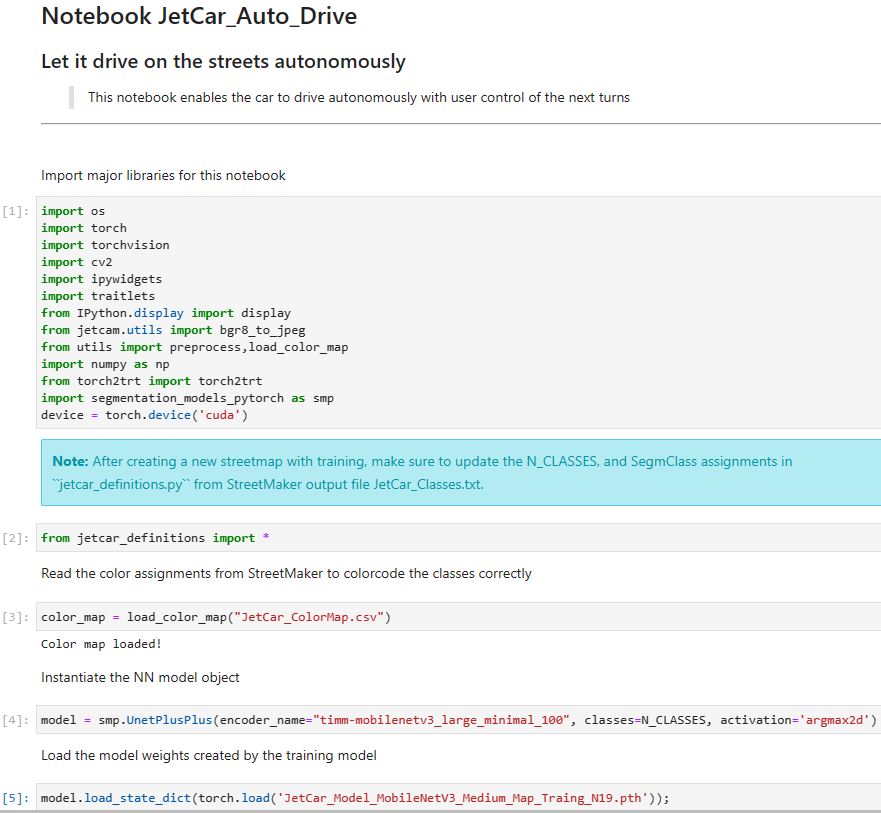
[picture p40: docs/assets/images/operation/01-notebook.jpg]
<br>
The self-driving functionality is implemented in the notebook <a href="https://github.com/StefansAI/JetCar/blob/main/firmware/jetcar/notebooks/JetCar_Auto_Drive.ipynb">JetCar_Auto_Drive.jpynb</a>. This notebook instantiates a couple of classes and GUI elements for visualization and control.
It utilizes widgets, arranges them in a display layout and defines event handlers.
<br><br>
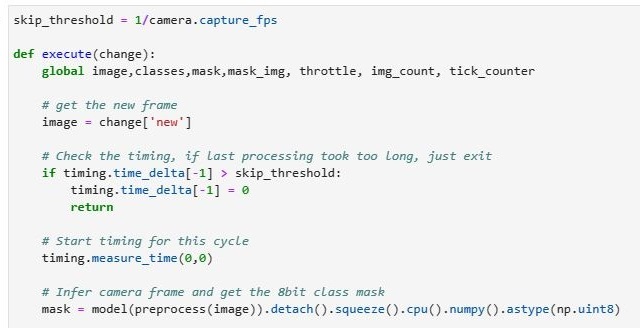
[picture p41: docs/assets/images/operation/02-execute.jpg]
<br>
But in the end it all comes down to this execute handler, which is called for each new frame from the camera. Right at the beginning after getting the camera image this function exits immediately, if the last cycle ran over its time limit. For real-time processing it is better to skip a data sample than starting to buffer and increasing the reaction time.
<br><br>
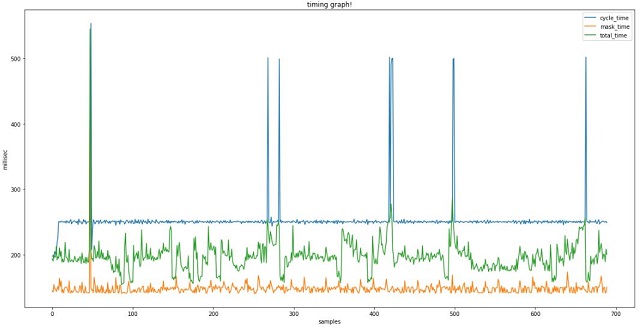
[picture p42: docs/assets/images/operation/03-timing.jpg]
<br>
A timing graph created from the SimpleTiming class logging shows, that the execution time occasionally spikes because of longer processing or because the system is busy. Skipping frames is essential to keep it in sync.
<br><br>
The core of the processing in the execute() handler comes down to the following:<br>

```Python
def execute(change):
    # get the new frame
    image = change['new']  
    
    # Infer camera frame and get the 8bit class mask
    mask = model(preprocess(image)).detach().squeeze().cpu().numpy().astype(np.uint8)

    # Now let the tracker object process the mask
    tracker.process(mask, next_turn_direction)

    # Pass on the steering and throttle values to the car object
    car.steering = tracker.steering_value
    car.throttle = tracker.throttle_value * throttle_value_slider.value
    
    # increment the image counter used in logging
    img_count += 1
    # Update turn signals and brake light
    car.signal_left = tracker.signal_left_enable & (img_count >>1 ) & 1
    car.signal_right = tracker.signal_right_enable & (img_count >>1 ) & 1
    car.brake_light = tracker.brake_light_enable
       
```
The mask is generated via model inference and then it is processed by the tracker object and its results are then passed on to the car.<br>
Let's dive deeper:
<br><br>
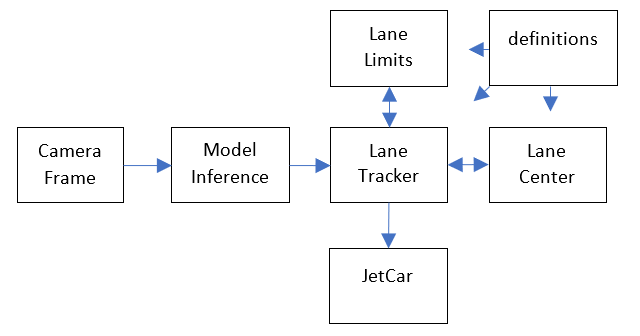
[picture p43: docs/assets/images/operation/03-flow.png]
<br>
This graph shows the data flow. The LaneTracker class in the file <a href="https://github.com/StefansAI/JetCar/blob/main/firmware/jetcar/notebooks/jetcar_tracker.pyhttps://github.com/StefansAI/JetCar/blob/main/firmware/jetcar/notebooks/jetc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">jetcar_tracker.py</a> now passes the mask on to its LaneLimits (<a href="https://github.com/StefansAI/JetCar/blob/main/firmware/jetcar/notebooks/jetcar_lane.py">jetcar_lane.py</a>) instances and after some preparations to LaneCenter (<a href="https://github.com/StefansAI/JetCar/blob/main/firmware/jetcar/notebooks/jetcar_center.py">jetcar_center.py</a>) instances. In the end, the LaneTracker class calculates new steering and throttle values and signals, which are then passed on to the JetCar class instance by the notebook to control the servo, the motors and the LEDs.
<br><br>
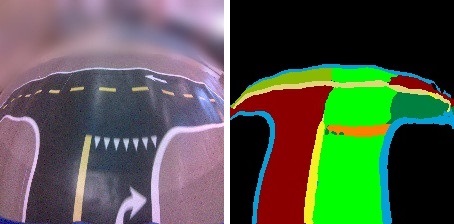
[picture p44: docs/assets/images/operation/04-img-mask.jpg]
<br>
On the left is a frame as it comes from the camera. It is very different from the artificial camera view generated by the StreetMaker. The paper with the printout isn't lying flat and shows some waves distorting the lines. And there are reflections from the ceiling lights and a lot of noise.<br>On the right the mask generated from the model inference. It is surprising, that it comes out pretty clean despite the imperfect input. <br>Just one the side: This example came from a debug run, where the model did not recognize the right turn arrow. That was fixed by collecting real images of arrows, run them through the ImageSegmenter and add them to the artificial dataset for the next training run together with adding view points.
<br><br>
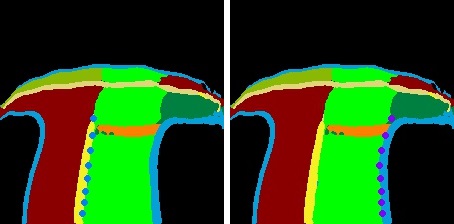
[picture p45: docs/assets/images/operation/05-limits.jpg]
<br>
The LaneTracker class first calls its get_lane_limits() method, which then calls find_limits() for lane_limits_left and lane_limits_right instances of the LaneLimit class. The find_limits() method searches in the mask for the lane limits left or right depending on the side. Each LaneLimit class owns its array of LaneLimitPoint instances. Their final locations after the search is shown above for the left and right objects.<br>
The search can take longer initially for the first frame. But after that the changes between frames are relatively small and the search is faster. 
<br><br>
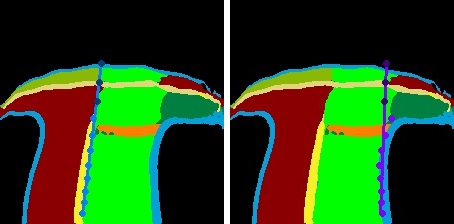
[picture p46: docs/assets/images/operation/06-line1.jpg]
<br>
The LaneLimit class then approximates a line through the found limit points and extrapolates additional point further out. <br>An originally implemented linear regression algorithm was occasionally too much effected by outliers. It sometimes resulted in almost horizontal lines. So, it had to be replaced with the current algorithm averaging the slopes between the points, which works better here.
<br><br>
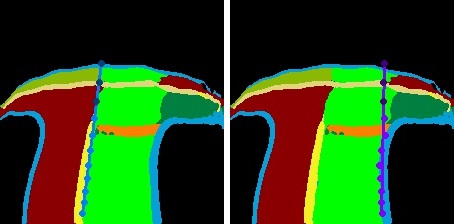
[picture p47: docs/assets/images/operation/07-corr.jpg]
<br>
Masks are not always as clean as this one. Sometimes outliers can be far out impacting the line approximation, which is used for the steering calculation later. So, the distance of each search point from the line is checked and outliers are adjusted in a second round. Here only one point on the right side above the yield line has been adjusted.
<br><br>
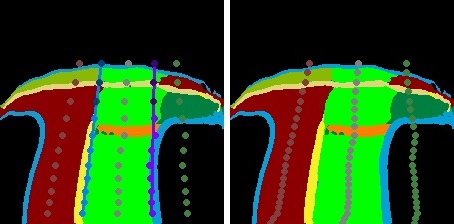
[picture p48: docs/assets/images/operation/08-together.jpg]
<br>
Back at the LaneTracker class, additional checks try to clean up more if the points are outside the expected lane width. It uses the standard deviations between points and line for each side to decide, if one side is too noisy to be trusted and might need correction. <br>
The masks above are very clean and there was no need. But it can happen, that there are false classifications or many artefacts in the mask. The whole processing has to be stable enough to figure out the most probable direction.<br>
The left side above now shows the final result of the left and right limits plus added points for the center of the driving lane and possible centers of the lanes left and right. The point arrays are passed to LaneCenter instances for left, center and right. More points are interpolated in between as seen on the right side. This gives now a very good sampling interval in each lane center. <br> To avoid relying on single point decisions, the dominant class codes around each point is determined. The dominant class is the one code in the pixel neighborhood, that appears most. A small artefact of few points can be suppressed this way.<br>
The next step in the LaneCenter class is run-length encoding of the classes in each direction for object tracking. Here are the RLE lists from this example:

| Left objects | Center objects | Right objects |
|---|---|---|
| | | 160:0:nothing:0:3 |
| | | 151:9:white_shoulder_line:0:3 |
| | | 141:10:lane_wrong_dir:0:3 |
| 164:0:nothing:0:3 | | 132:9:yellow_dashed_line:0:3  |
| 155:9:lane_left_turn:0:3 | 160:0:nothing:0:3 | 114:18:lane_right_turn:0:3 |
| 145:10:yellow_dashed_line:0:3 | 141:10:yellow_dashed_line:0:3 | 105:9:white_shoulder_line:0:3 |
| 0:145:lane_wrong_dir:0:3 | 88:9:yield_line:0:3 | 0:105:nothing:0:3 |
<br>

Let's look at the left list. It is sorted from close to the car at the bottom to far out at the top. It starts with 0:145:lane_wrong_dir, which means there is a class code for wrong direction starting at distance=0 with a length of 145. In an image of 224x224 this object stretches into the top half and that is exactly what we can see. Then there is a yellow dashed line, followed by a left turn lane and then nothing.<br>
In the center lane, the driving direction code is dropped, because it is assumed to be there. So, the list starts with the yield line, then the yellow dashed line again and nothing at the end.<br>
On the right side there is nothing at the beginning for a long stretch, but then a lot of different class codes.
<br>
Now let's look at the tracking part:

| Left objects | Center objects | Right objects |
|---|---|---|
| | | 160:0:nothing:2:3 |
| | | 151:9:white_shoulder_line:1:3 |
| 165:1:nothing:1:3 | | 141:10:lane_wrong_dir:2:3 |
| 165:0:white_shoulder_line:2:1 | | 132:9:yellow_dashed_line:2:3  |
| 156:9:lane_left_turn:5:3 | 160:0:white_shoulder_line:1:2 | 114:18:lane_right_turn:3:3 |
| 146:10:yellow_dashed_line:3:3 | 141:10:yellow_dashed_line:5:3 | 105:9:white_shoulder_line:2:3 |
| -38:144:lane_wrong_dir:17:3 | 88:9:yield_line:7:3 | -58:163:nothing:17:3 |
<br>

The new RLE lists are now merged with the tracking lists. The algorithm tries to match new list and tracking list items. When a match is found, the starting point and the length (or size) are updated. There are more items in the lists than in the new lists, which means that there are objects sampled before. As stated above, the 2 numbers in front of the class code name are distance:length. The 2 numbers after are alive:ttl. The alive-number is increased with each cycle this object is tracked in the list. The ttl-number (Time-To-Live) is decremented each time this object does not appear in a new list. When reached 0, this object entry will be removed from the list. This ensures, that any artefacts are cleaned up. In the example above, the white shoulder line entry might disappear in the next cycle, if it is not detected again. In this case, the detection was correct, but just too far out and too small at this point. When it comes closer, it might be re-introduced again.<br>
If the alive-number is low, the probability of this entry beeing a false detection is still high. A high number on the other side clearly states that this is very real. The LaneTracker class, can now make decisions with these entries. It can check distance, size (length) and alive count to react on it. For instance a right turn should wait until the right turn lane is close enough, more than a few pixel wide and tracked for some time to start the turn. In this example, those conditions are not met yet.<br>
One more comment about the negative distances in the lists above. The distance of 0 starts at the number and increases from there out to the front. A negative value would indicate something under the car or behind. The camera would not be able to see it, so why is it kept in the list?<br>
When approaching an intersection, there might be a left turn only arrow or a stop text. But getting closer to entering the intersection or at the stop line, it is already out of sight. Those objects will have to be kept in the lists to make the correct turn or to make a stop correctly. After the turn or passing the intersection, those entries need to be cleaned up via special calls.<br>
The cleanup also sets the flags that all directions are allowed for the next intersection to come. Whenever an arrow appears, these flags are updated accordingly. So, when the next left or right turn code comes up and a direction was requested, these flags are checked before a turn can be initiated.<br>
It can be imagined, that there are a lot of conditions to be checked while driving. The process() method of the LaneTracker class contains many if-statements to make it work. And there are many defined thresholds, that worked for tested conditions. But real-world/real-time conditions might still cause the car making wrong decisions. Fortunately, nobody will be run over by a toy car and you can play around with the code to find better solutions.<br><br>
Implementing a stop is relatively easy. Just keep the throttle at 0 for a bit and it looks like a stop. No traffic is expected at this point :-). So, a stop counter will do just fine.<br>
Turning is a different problem. The lane ahead is our driving lane and the turn lane might be coded left turn or right turn lane. What happens while turning? The answer is: Chaos.
<br><br>
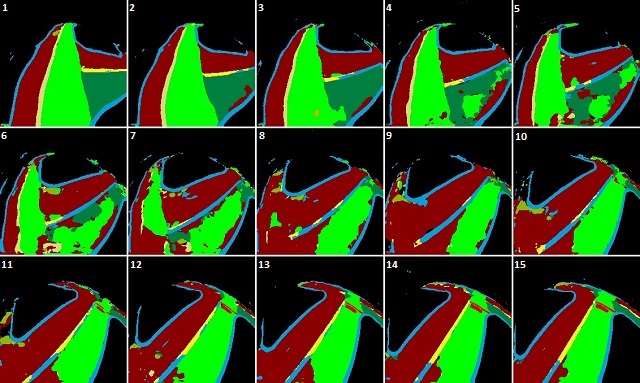
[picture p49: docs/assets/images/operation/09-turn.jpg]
<br>
Above is a sequence of masks recorded in a right turn. As can be seen, in a turn the classification of pixels has to change from right turn (olive green) to my driving direction (green), but the transition creates a lot of artefacts and even wrong classifications. To overcome this, the steering is set to a turn and the masks are simply not processed for a few frames. It can be compared to our driving, when we start turning the wheel to some estimated turn radius and hold it until we can straighten it out again. Of course, we constantly check, if we need to correct. So, the JetCar will do something similar. It will initiate a turn, setting the steering to a fixed value. It will then ignore the masks for few cycles and then start tracking again. In the sequence above for instance it can ignore the masks from frame 1 to 7 after the turn, but frame 8 might give results good enough in the diagonal to start tracking again. It can keep turning, but start correcting the steering to get the car aligned.<br>
In the implementation the LaneTracker class owns a steering_fixed_count, which is set to a positive value when the turn is initiated. The steering value is not changed and anything is ignored for a few frames. But with each new frame it will be decremented and about half way through to 0, the limit search is enabled again and steering values are calculated. If it is getting closer to alignment in about +/-45 degree in front, the counter is set to 0 and operation resumes normally. Otherwise the fixed turn continues until it reached 0 and the steering resumes from there.
<br><br><br>

- <a href="Data%20Preparation.md">Data Preparation with ImageSegmenter</a><br>
- <a href="Model%20Training.md">Model Training</a><br>
- <a href="StreetMaker.md">Street Maker</a><br>
- <a href="Debugging.md">Debugging</a><br>

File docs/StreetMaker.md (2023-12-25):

<h1 style="text-align: center;">JetCar</h1>
<h2 style="text-align: center;">StreetMaker</h2>
<br><br>
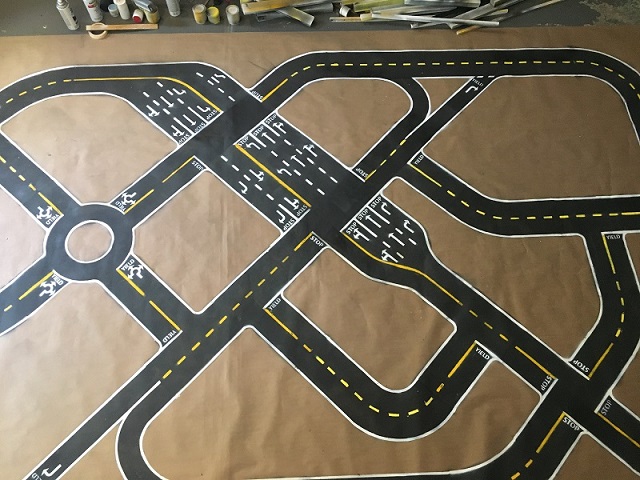
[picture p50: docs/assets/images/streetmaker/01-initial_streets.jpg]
<br>
Making a street map with a lot of different templates, cut out of paper and hours of spray painting is a lot of work. It turned out to be too large to spread it out, when the garage had to be used for those big cars. :-(<br>
Something new was needed to create a street map in a much simpler way and could possibly do much more ...
<br><br>
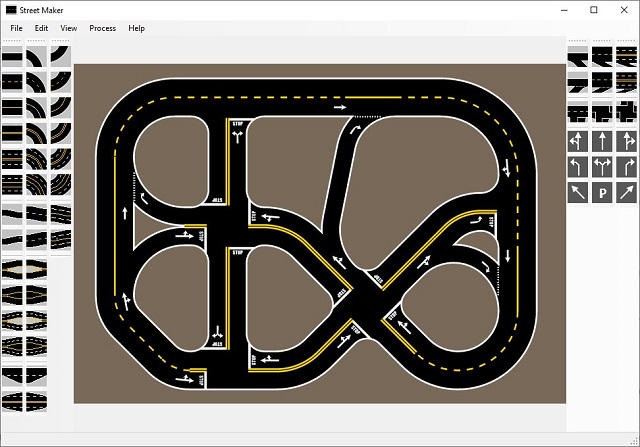
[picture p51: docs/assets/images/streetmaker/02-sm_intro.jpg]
<br><br>
This application is part of this repository. You can find the <a href="https://github.com/StefansAI/JetCar/tree/main/tools/bin/StreetMaker">executable</a> and the <a href="https://github.com/StefansAI/JetCar/tree/main/tools/source/StreetMaker">full source code</a> in the tools folder. <br>
In the middle of the screen is the map area. On the left side is a tool bar with different street segments and on the right with intersections and overlays.
<br><br>
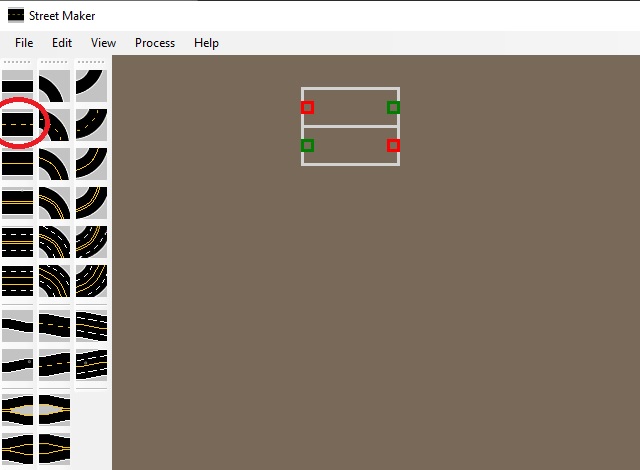
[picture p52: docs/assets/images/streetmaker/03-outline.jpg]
<br><br>
To start creating a new map, simply click on one of the tool buttons and then move the mouse over to the map. The outline appears with red and green connector boxes indicating in and out of the lanes.
<br><br>
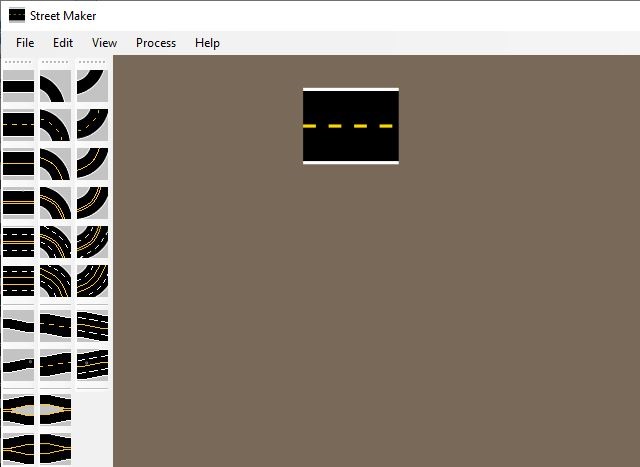
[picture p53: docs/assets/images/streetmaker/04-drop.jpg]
<br><br>
Click on the map to drop it there.
<br><br>
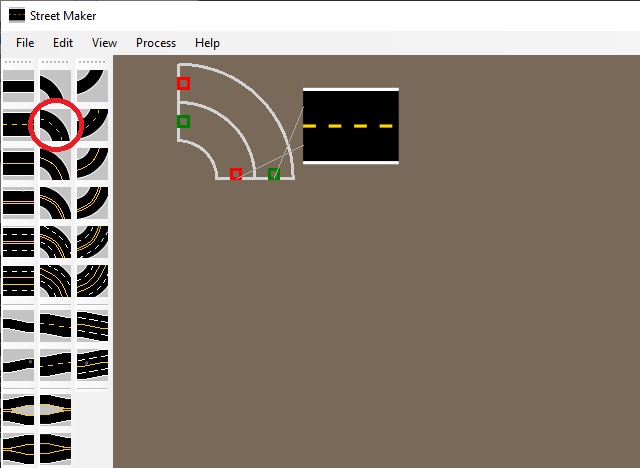
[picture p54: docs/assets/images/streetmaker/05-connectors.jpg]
<br><br>
Grab a curve piece and when moving over, lines appear to show where it can click together.
<br><br>
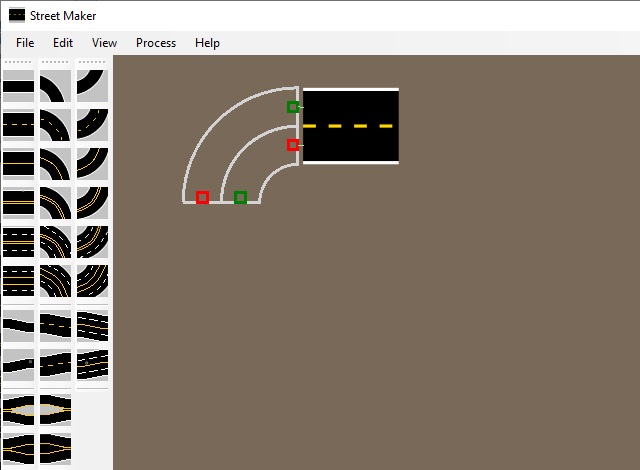
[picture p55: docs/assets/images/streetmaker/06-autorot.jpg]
<br><br>
When getting the possible connectors even closer together, the curved segment auto rotates and can be moved into position. It can be also manually rotated with the hotkeys "R" to the right and "E" to the left.
<br><br>
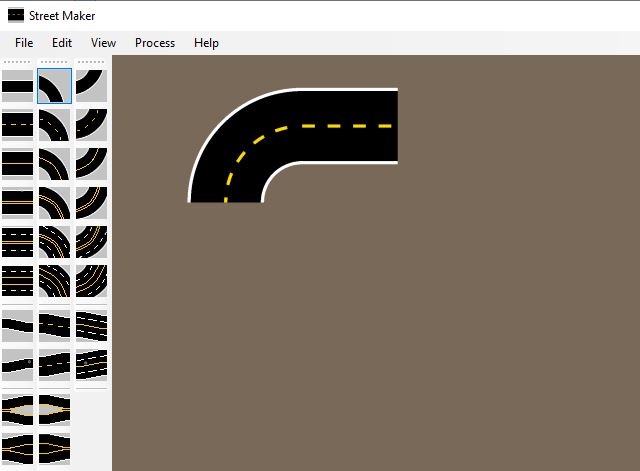
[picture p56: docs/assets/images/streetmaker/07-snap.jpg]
<br><br>
Left mouse click snaps them together and they are now connected.
<br><br>
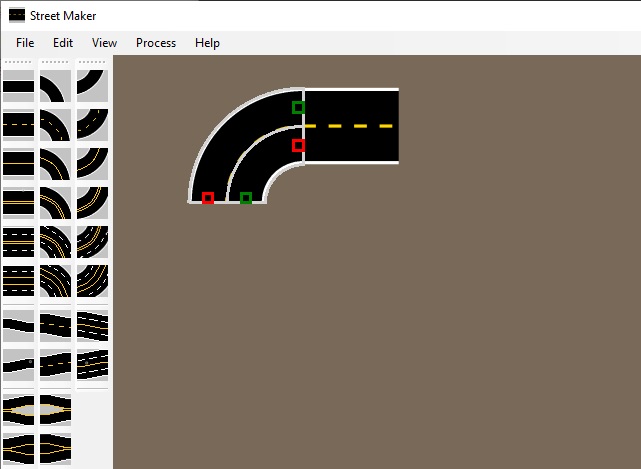
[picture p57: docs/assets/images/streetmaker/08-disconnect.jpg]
<br><br>
To disconnect any street element, simply hover the mouse over the element and hit "D" for disconnect.
<br><br>
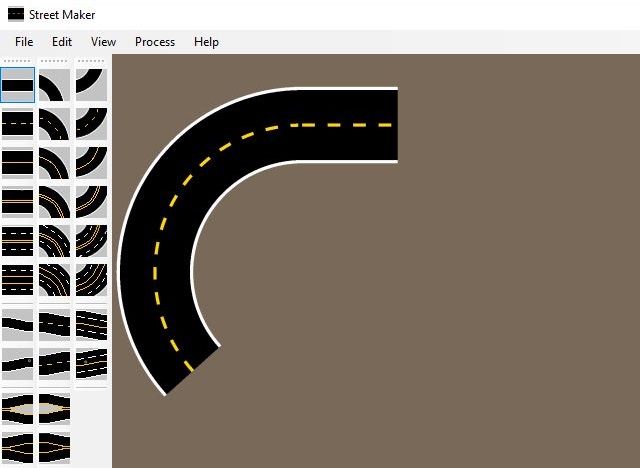
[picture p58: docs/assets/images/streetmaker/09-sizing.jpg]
<br><br>
When hovering for instance over the lower left red connector, pressing "S" for sizing, left mouse clicking and dragging the connector, the curve gets more or less bend around. The angle changes but the radius stays the same.<br>
Pressing "A" instead of "S", left mouse click and drag will result in radius and angle getting changed.
<br><br>
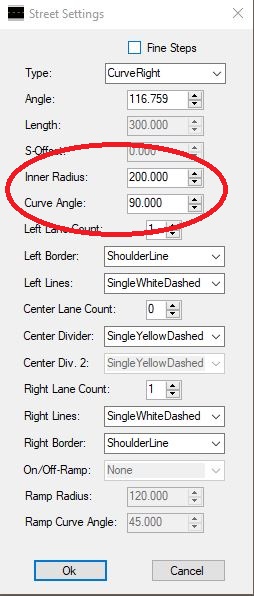
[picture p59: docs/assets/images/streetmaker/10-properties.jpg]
<br><br>
Right clicking on any street element brings up its property page dialog as seen here for the curve piece. Change the "Inner Radius" to 200mm and the "Curve Angle" to 90 degrees for instance.<br>
There are many other parameters to change for each street element, like number of lanes in both directions and the limiting lines. In fact, each street can even be changed into any other street, except into intersections. Any intersection type can also be changed into any other intersection type, but not into a street element.<br>
After the change the curve might be separated from the straight street. Each element has a starting point as reference and changes are made to that reference, which might cause it to shorten or lengthen on the other side.
<br><br>
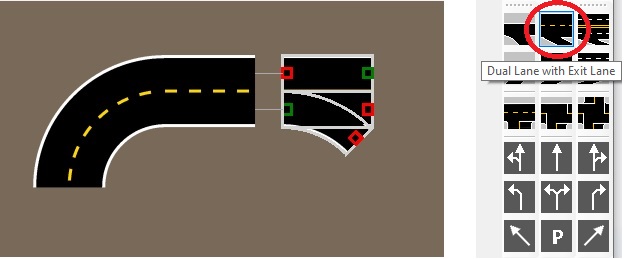
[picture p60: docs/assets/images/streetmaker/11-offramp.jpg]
<br><br>
Add a "Dual Lane with Exit" from the right side. It can also be seen as an off-ramp. Open the property page and change the "Length" to 540mm and the "Ramp Curve Angle" to 90 degrees.
<br><br>
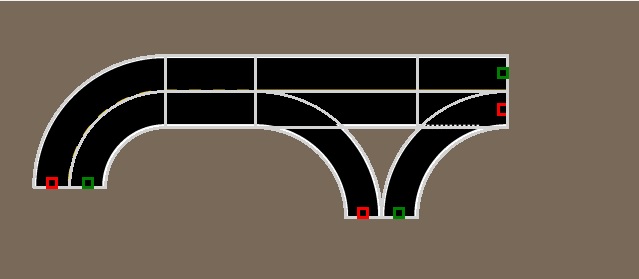
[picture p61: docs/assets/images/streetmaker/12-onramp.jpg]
<br><br>
Add a "Dual Lane with Junction Lane", that looks like an on-ramp and change its "Ramp Curve Angle" to 90 degrees. It looks perfect for adding a dual lane below. Why the length of 540mm above? The "Ramp Radius" was 300mm and the lane width 120mm, but the on-ramp adds another lane width, so 540 together.
<br><br>
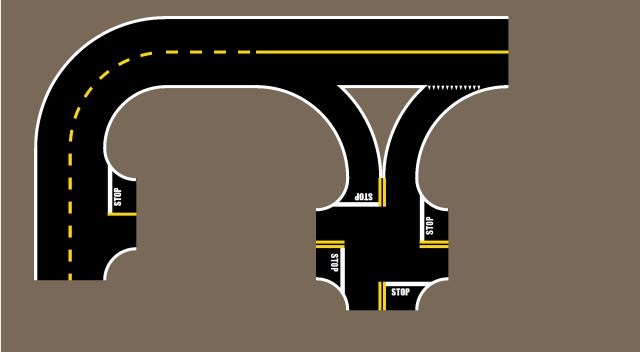
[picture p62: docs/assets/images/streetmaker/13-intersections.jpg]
<br><br>
Add a "T-Intersection" on the left and a "4-Way-Intersection" on the right and should look like this. There are different ways to connect the 2 intersections. 
<br><br>
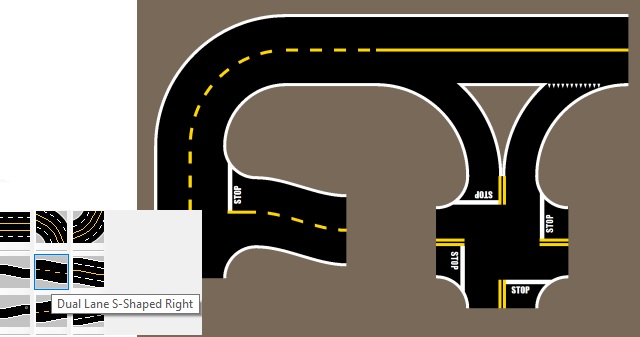
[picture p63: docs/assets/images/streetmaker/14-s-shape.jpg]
<br><br>
The simple one is using a "Dual Lane S-shaped Right". Connect it the the left.
<br><br>
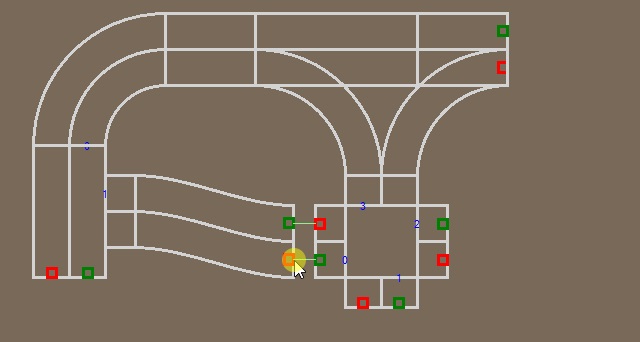
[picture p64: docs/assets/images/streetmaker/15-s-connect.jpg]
<br><br>
Use the hot key "A" when grabbing a connector on the right to drag it to the right intersection close enough to let them snap together. Using an S-shaped street can always be used to connect any offset elements easily.
<br><br>
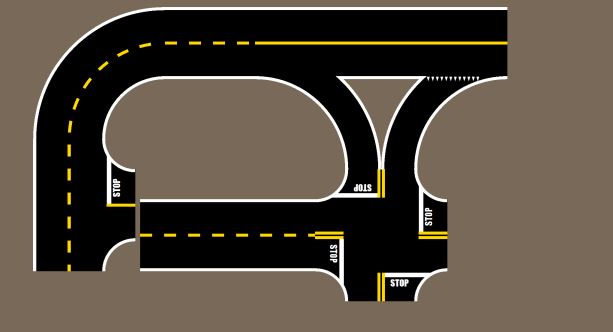
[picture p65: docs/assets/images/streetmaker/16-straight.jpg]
<br><br>
The other method is following: Add straight streets close enough for instance.
<br><br>
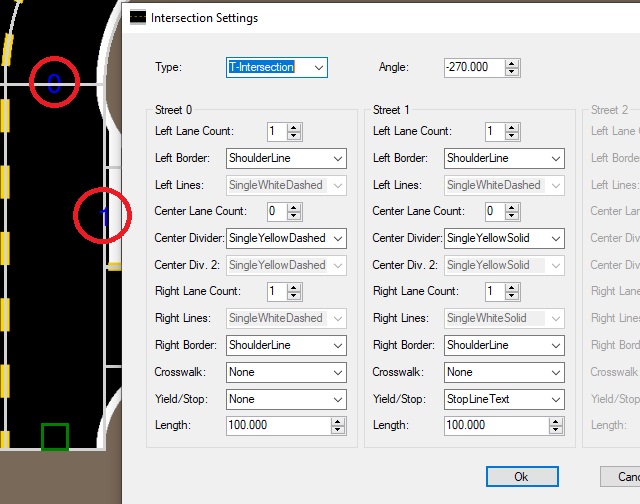
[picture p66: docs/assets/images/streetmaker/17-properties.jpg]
<br><br>
Now open the property dialog of the T-Intersection. The entering streets are indexed and the numbering appears with the outline when hovering over the intersection. In this case, the length of "Street 0" can be adjusted to shift "Street 1" down closer to the desired connection.<br>
Set "Street 0" length to 200mm.
<br><br>
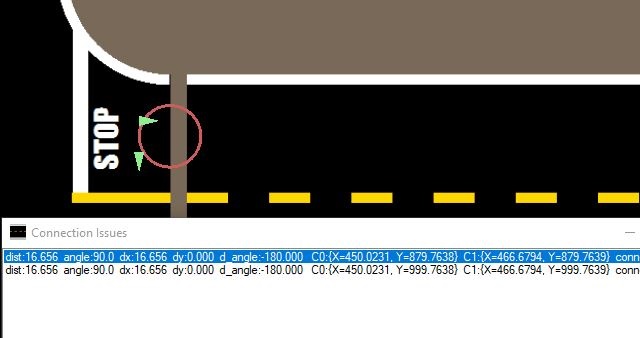
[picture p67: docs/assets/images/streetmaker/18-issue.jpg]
<br><br>
A message shows up informing about 2 connection issues. This will always come up, whenever connectors are close, but cannot be snapped together. When clicking on any item in the list, the location will be shown and what direction should be any corretion. Here it shows a dx=16.656mm and dy=0. The angle difference between the 2 connectors shows d_angle=-180, which is no problem and neither is dy. So, we only need to add 16.656mm to the intersection or to the straight street to close the gap.<br>
This can be done via the property dialogs of either one, or via sizing the street length via mouse and hotkey "S". The last method might require a disconnect via "D" first to be able to grab a connector.<br>
If dx and dy are both not zero, then it is often necessary to go back and forth between the property dialogs of both elements to get them close enough. If the d_angle value is something other than 0 or +-180, it will get more difficult. Then there might be a curve angle somewhere in the chain to be corrected.
<br><br>
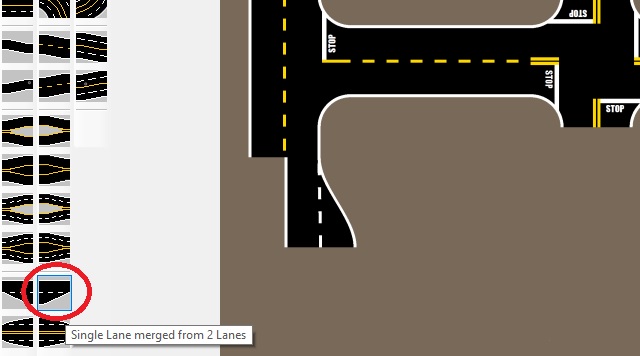
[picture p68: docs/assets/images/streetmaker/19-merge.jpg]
<br><br>
Lets add a merging element and change the "Left Lane Count" from 0 to 1 and the "Center Divider: to "SingleYellowDashed". Then add "Single Lane expanded.." and apply the same changes.
<br><br>
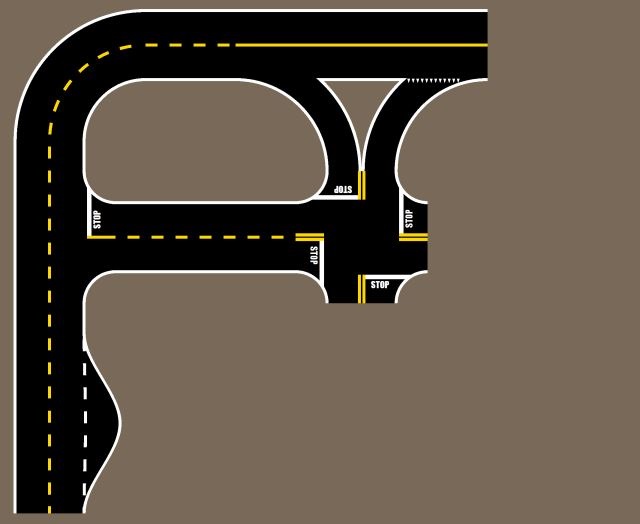
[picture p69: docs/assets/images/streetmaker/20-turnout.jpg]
<br><br>
Together, this created a turnout for a parking area. But of course, new street elements with double lanes on that side could have been used to enter end exit a multi-lane segment.
<br><br>
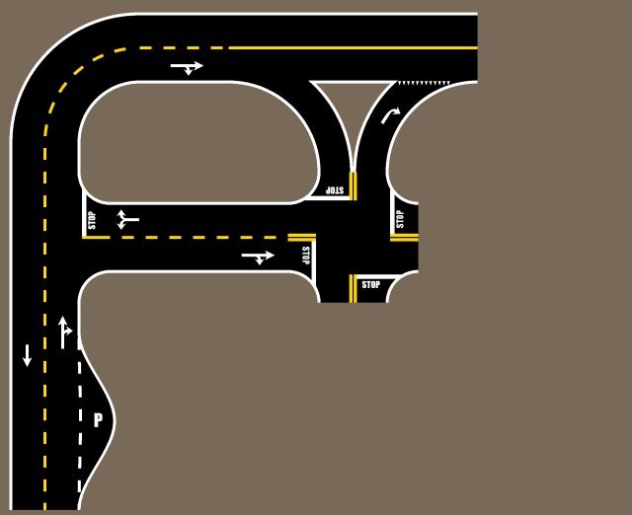
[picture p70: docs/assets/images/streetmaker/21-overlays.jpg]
<br><br>
Now grab some street signs, like different arrows from the right and drop them at intersections. They will automatically be centered in the lane and aligned with the correct direction.
<br><br>
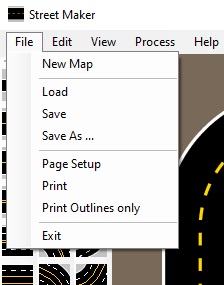
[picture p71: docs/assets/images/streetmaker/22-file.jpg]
<br><br>
It's time to check on the menus. Open "File" and "Save" this map for continuing later via "Load". <br>"New Map" will start with a clear area of a choosable size.<br>
Of course printing this map is possible from here too. Despite setting for instance a 1-inch margin in the "Page Setup" dialog all around, the printer might do it only on top and left, while the bottom and right margins end up smaller. To test out the printer without wasting colors, the "Print Outlines only" can be used. "Print" will send all pages in color.
<br><br>
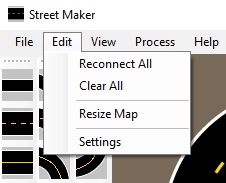
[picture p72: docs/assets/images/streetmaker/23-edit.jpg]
<br><br>
The "Edit" menu contains some special case items easily to guess from the texts. Let's have a look at "Settings".
<br><br>
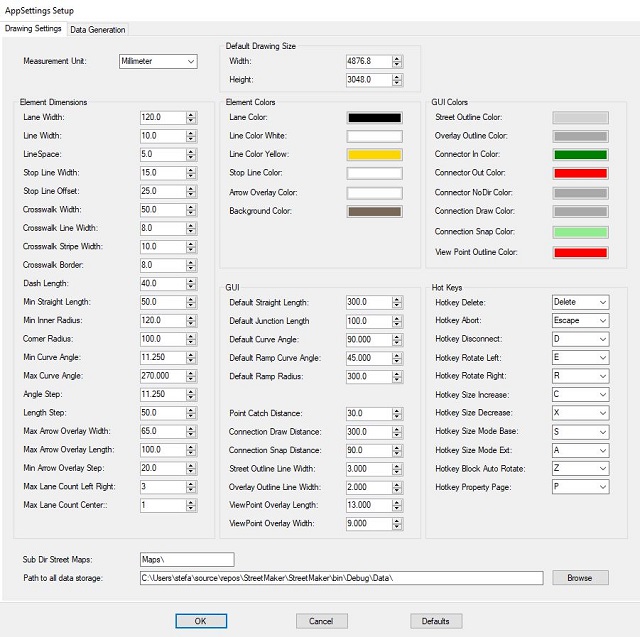
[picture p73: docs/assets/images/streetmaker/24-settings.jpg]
<br><br>
This dialog is pretty packed. But you normally won't have to change anything, except you want to tally customize it in a different way. First, the is the "Measurement Unit" right at the top to set to any standard or imperial. All related values will be converted automatically.<br><br>
The hot keys are listed on the right side and can be changed there to.<br>
Let's close it for now and continue.
<br><br>
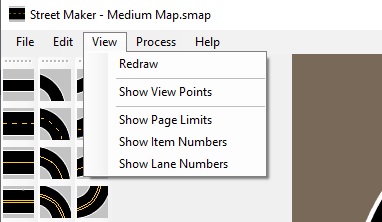
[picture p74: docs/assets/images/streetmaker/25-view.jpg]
<br><br>
Whenever there are some drawing artefacts left from ovberlapping elements while placing them, the "Redraw" menu item will farce a complete new drawing of the map, clearing it from artefacts.<br>
Let's ignore "Show View Points" for now. It will be explained further down.<br>
"Show Page Limits" can help to determine the number of needed print pages in width and height and to center the map.<br>
"Show Item Numbers" and "Show Lane numbers" can be used for any identification for troubleshooting by overlaying the index of each street element in the internal list and the lane index of each street or intersection.
<br><br>
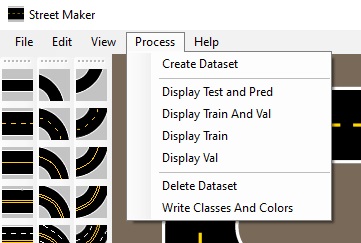
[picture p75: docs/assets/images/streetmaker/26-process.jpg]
<br><br>
When opening the "Process" menu, it might be surprising to see menu items similar to the ImageSegmenter application described before. As it turned out, when writing the StreetMaker application, most of the information needed for creating segmentation masks was already there. Connectors kept track of the directions and lines can be selected by type. The drawing area is a bird's eye view on the street map. What was needed was a camera view, a camera view of a wide-angle camera with lens distortion from a certain height above the ground looking forward in a defined angle on the same map from a specific point of view.
<br><br>
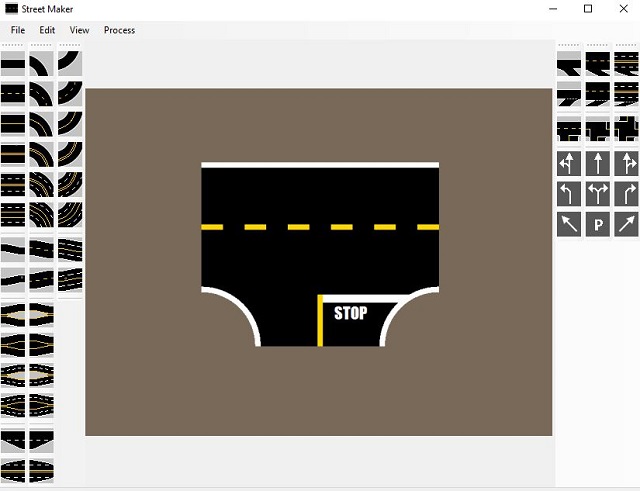
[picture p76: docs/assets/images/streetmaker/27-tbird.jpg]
<br><br>
Let's start a new map and just put a T-Intersection on a new map. Now let's see what dataset would be created when hitting "Create Dataset". 
<br><br>
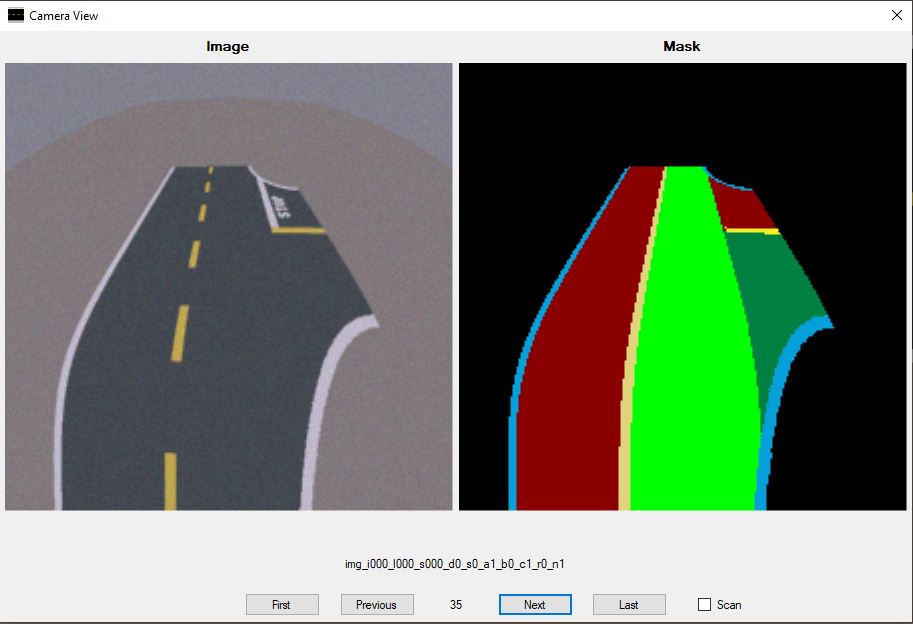
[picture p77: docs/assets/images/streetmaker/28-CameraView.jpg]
<br><br>
Similar to the ImageSegmenter application you can see, how different tilts, brightness values and noise levels are applied, while the view seems to go forward and backwards. On the left side an artificial camera view is displayed, while a mask appears on the right side.<br>
Of course, the camera view is totally artificial. It still misses effects of a real scene. But it is close enough for training a model, that might need only few additional real photos and masks from the ImageSegementer. 
<br><br>
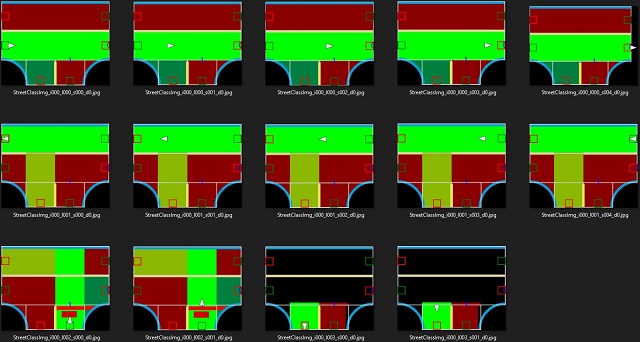
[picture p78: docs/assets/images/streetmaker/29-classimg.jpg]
<br><br>
Here is an illustration on how the algorithm works. The white triangle represents the camera point and direction. It starts with lane 0 of street 0 close to the entry connector and goes forward to the end. Then it goes backwards on the other side. After that it repeats this scheme for the second street.<br>
Of course, the camera point will always be on the lane it drives, so it should be the driving direction lane and the other side the wrong lane. Left and right turns are added depending on the view direction.
<br><br>
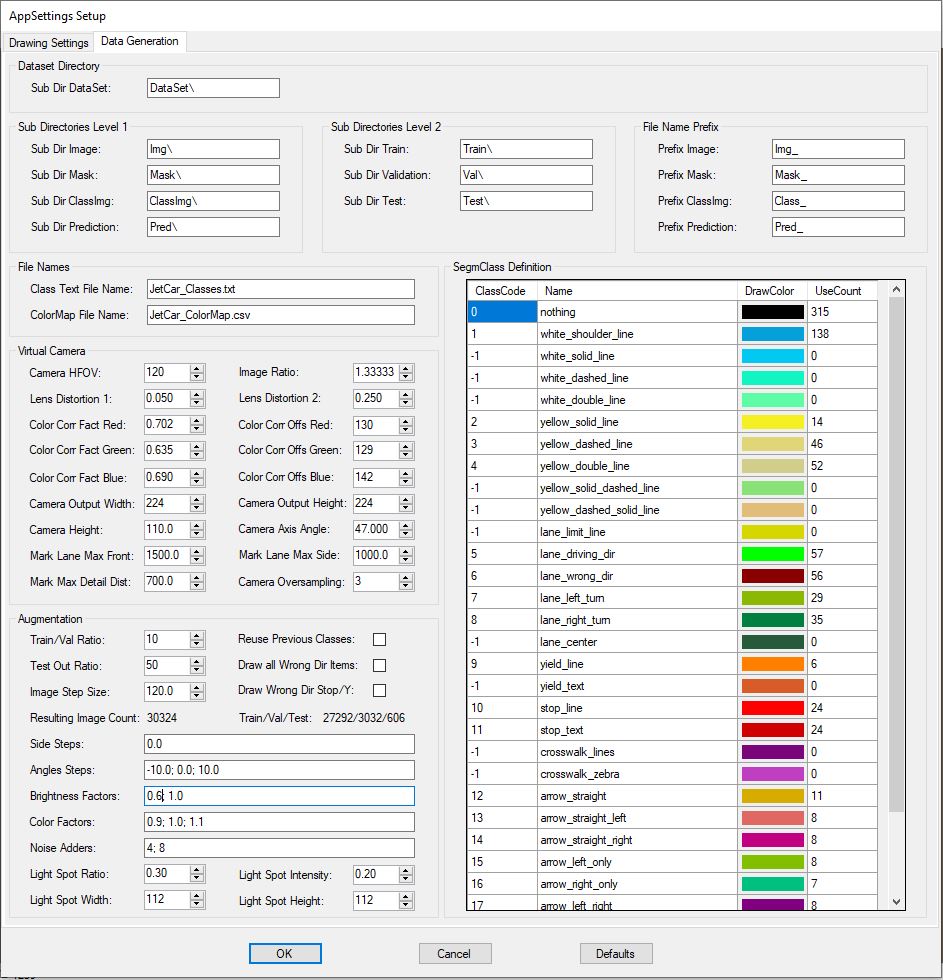
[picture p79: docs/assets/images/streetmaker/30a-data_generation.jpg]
<br><br>
Understanding the dataset creation in StreetMaker will make it clearer to look at the "Data Generation" page of the "Settings" dialog. Besides similar folder and subfolder structure and class definitions as in ImageSegementer, there are a number of parameters around the virtual camera geometry. Unless there is a real need for a complete customization, it will not be necessary to change.<br>
Even if it says 120 degrees of horizontal field of view for the camera and the actual camera module in the JetCar design states 145 degree, don't try to adjust it. When dealing with optical system for a long time, you'll have to accept that specifically wide-angle lenses have their own rules because of the distortion. 120 can be seen as nominal and 145 after distortion. The optical simulation here was also simplified.<br>
Besides geometrical distortion, there are fields for color distortion. When the camera looks at a printout of a specific color, it does not see the same as the color printed out. Experimentally the overall brightness factor came out around 80%, but the red color was much higher around 95%. That's why there are 3 color correction values for creating a camera view image. A different camera and different lighting may result in other factors.<br>
The last parameter "Mark Lane Max Front", "Mark Lane Max Side" and "Mask Max Detail Dist." determine how far out or to the side anything is represented in the mask and how far overlay details are generated. It doesn't make too much sense to train on a few pixels arrow or even a street far out. These limits create some kind of horizon for the mask.<br>
The augmentation area shows similar parameter fields as in the ImageSegmenter and similar multiplication rules apply when adding more values. But there is also an "Image Step Size". This is exactly the step size moving the camera forward or backwards as described in the previous images above. Increasing this number will reduce the number of images in the dataset and decreasing the step size will result in more.<br>
<br><br>
If a street map is loaded, the program calculates the number of image/mask pairs that will be generated with the current parameter. It will be updated after changing step size or any of the augmentation parameters.<br>
There are some more checkboxes to be ignored for now, since they were introduced for testing different options. But the defaults are good to go.<br>
Below the augmentation settings there are few more parameter to simulate light spots.
<br>
<br><br>
While testing the JetCar on the printed out map, it turned out that light reflexions disturbed the camera image quiet often and caused bad classification spots in the resulting mask.
<br><br>
One way to avoid this is creating a diffuse light, blocking sun light from windows and use less reflective paper for the printout. A matte thick paper (second picture) works much better than the standard printer paper, which is often glossy and thin (first picture). Thick is better to keep the paper flat.<br>
But on top of it all, just add light-spots into the training and testing dataset. With these parameters a light spot is overlaid to 30% of all output images with randomized size and intensity around these settings (+/- 50%). This helps to harden the model against remaining light spots in the scene.<br>
<br>
<br><br>
The class definition table on the right side of this dialog is a bit different than the one in the ImageSegmenter not only because more class possibilities were introduced with StreetMaker, like crosswalks. Some items were also renamed slightly. But the column "UseCount" hints to another feature of this application. It will always optimize the class output to what is actually used in the particular street map. Every UseCount of 0 will be removed from the ClassCode enumeration. Note that the ClassCode is set to -1 for each class that is not used. This will result in an optimal set of classes for each individual map, which is more efficient for run-time execution but worse for exchangeability of model weights between different maps. The compromise is training on a map with more classes used, but printing maps with subsets of that training map. <br>
Let's have a look at the "File Names" group. When generating a new dataset, these 2 files are generated too and written to the data path.
<br><br>
<br><br>
Opening the file "JetCar_Classes.txt" shows 2 parts: The top part can be copied directly into the file "JetCar_definitions.py" inside the Jetson Nano on the JetCar to overwrite the existing definitions.<br>
The bottom part can be copied into the file "ImageSegmenter.Cfg" file to overwrite the class definitions there. This allows taking real images of the printed streetmap, marking the same classes and mixing them together with the StreetMaker datasets to increase accuracy for the training.
<br><br>
<br><br>
The second file generated with each new dataset is the "JetCar_ColorMap.csv". This file can be directly copied to the JetCar notebook work space. It will make sure the same colors appear in the mask on the screen as defined in StreetMaker. Since the class codes are changing, this color map will ensure, the appearance will not.<br>Note: The color order is reversed for the python libraries to BGR instead of the usual RGB.
<br><br>
<br><br>
With all discussed above, you can knock yourself out and create a nice large map like this one and buy some packages of paper. This one will consume 13x14=182 sheets of A3 paper or 17x11 and is about 4.9x3.2 meter or 16x10.4 feet big. But it doesn't even contain center lanes or crosswalks. <br>
The problem at this point is, that the StreetMaker can generate scenes, which the firmware currently does not yet handle. The JetCar code will have to catch up to that. <br>
It can be imagined that at some point later the map should be integrated into the code like a phone map and the car should find it's own way for instance from any given point to a specific parking space as a destination point. Something for the next extensions.
<br><br><br>

<mark>REMARK</mark><br><br>

If you have a new map you want to train on, it might happen that some classes appear only once or very few times. After running the model training on datasets, these few classes might be not recognized in the inference. When that happens you can take real images of these classes, run them through ImageSegmenter and merge the dataset with the streetmaker dataset for the next training run.<br>
Alternatively you can increase the occurance of these classes.
<br><br>
<br><br>
Here is a medium sized map, ready for print out.
<br><br>
<br><br>
Opening the settings dialog reveals, that for instance the "arrow_left_only" appears just one time and the "arrow_left_right" only two times.
<br><br>
<br><br>
To increase the occurances, you could copy the map to have one for print out and one for training. In the training map you could just sprinkle more arrows on the streets to increase their numbers.<br>
But the "yield_line" had also a low occurance, which cannot be solved this way.
<br><br>
<br><br>
Alternatively you can just enlarge the training map and add more street elements and overlays there. The added streets don't have to make real sense as a map, they are just there to create more images and masks in the dataset for training on these classes.
<br><br>
<br><br>
With this training map, the number of occurances look better than before, but it is still not the best solution.
<br><br>
<br><br>
Let's get back to the menu item "Show View Points". When checking it, a new overlay is enabled, that wasn't there before.<br>
Adding this "View Point" to the street map gives you more control over the dataset generation for the model training.<br><br>
<br><br>
When looking at the medium training map after turning on the view points, a number of small red outlined triangles become visible. When generating the dataset, it will be checked if a lane element had viewpoints assigned or not. If yes, only these view points will be used to generate image/mask pairs for the dataset. If none are assigned, image/mask pairs are generated automatically along the lane element using the step size.<br><br>
<br><br>
View points can be placed strategically to generate clear views on details, like this arrow and the intersection. Double click on the view point and the virtual camera view comes up.<br><br>
<br><br>
The complete arrow is in full view and not a fraction of it. Just imagine, the automatic view placement would have ended up showing just the arrow tip and training the model on the straight-right-arrow class. It might later confuse every arrow tip as that class, even if it is just a straight arrow or a straight-left-arrow.<br><br>
<br><br>
Here is another example of a placement with unwanted results. If the automatic algorithm placed the point just at the end of the intersection, another training problem can occur.<br><br>
<br><br>
At the bottom right of this view there is the artefact of the last piece of intersection with the wrong-direction class code, but the white line in the view.<br> 
Part of the problem is suppressing all marking on wrong-dir-lanes, which suppressed the stop-line class here. But the line is also recessed and the wrong-dir code will still show up around it.<br>
This problem occured often enough with automatic view generation, that wrong-dir artefacts showed up between shoulder line class and driving direction class at inference. Placing the view points correctly will avoid this completely. <br><br>
<br><br>
The picture above shows the placement around one intersection. Several view points had been placed before arrows to enhance the training on the arrows and intersections. View points directly at the stop signs will improve their training. View points at the interscetion exit lanes are placed behind the curves to avoid the artefacts shown above.
<br><br>
<br><br>
The training will result in a prediction using the test data input. Unzip the prediction results into the dataset folder.<br><br>
<br><br>
These PNG files don't display well in the file explorer view, since the few encoded classes come up as very dark gray tones only.<br><br>
<br><br>
But they can be visualized via the StreetMaker application using the "Display Test and Pred" menu item.<br><br>
<br><br>
This opens the camera view form displaying the image, the mask and the prediction result together. The cursor can be moved over either one of them to display the codes at the cursor position. If the mask and prediction classes match, the texts appear in black. If they don't match, the text color is changed to red.<br><br>
<br><br>
If you want to check the prediction results from two different training runs, just place the previous version into a folder named "*Cmp" next to the prediction folder.<br><br>
<br><br>
In this case, the camera view form displays the additional compare contents on the right side. Now it can be checked, if the new run had better results then the previous one. Of course, this only works when the same dataset was used in both. Otherwise the names would not match up.<br><br>
<br><br>
Because the ImageSegmenter uses a slightly different naming scheme for the dataset than the StreetMaker, both can be easily mixed together to create one dataset for training and prediction. The StreetMaker application can display both results as shown above. The camera image on the left shows clearly where the printed papers were glued together. Unfortunately the color tones changed from one printed row to the next. But the results were still acceptable.
<br><br>
Mixing both together will definitely help bridging the virtual world of the StreetMaker with real scene photos used for the ImageSegmenter. As you can see above, despite all efforts to create good virtual images, real camera images look quiete different. There are the different print colors, the seems and also the background that can confuse the model.
<br><br><br>

- <a href="Data%20Preparation.md">Data Preparation with ImageSegmenter</a><br>
- <a href="Operation.md">Operation</a><br>

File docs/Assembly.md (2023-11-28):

<h1 style="text-align: center;">JetCar</h1>
<h2 style="text-align: center;">Assembly</h2>
<br><br>
<br>
Get the parts from the 3D printer, remove the support layers and clean up the parts, sand them where necessary and make them smooth for assembly.
<br><br>
<br><br>
Start with the undercarriage and the steering parts. Place the wheel spindles on the undercarriage and make sure, they move and don't grind. File, sand or use drill bits where necessary to make them fit snug and smooth.
<br><br>
<br><br>
Place the steering rack part and the front axle part on top of the wheel spindles and make sure again, it moves smoothly.
<br><br>
<br><br>
Screw the front axle to the undercarriage with the taping screws. Check afterwards that the steering parts move smoothly.
<br><br>
<br><br>
Now, screw the servo controller to the undercarriage. Find more info about the servo controller here:  <a href="https://learn.adafruit.com/16-channel-pwm-servo-driver/downloads">Schematics</a> 
<br><br>
<br><br>
Solder wires with connectors to the motors and to the H-bridge boards and slide the H-bridges in place. <a href="https://www.ti.com/lit/ds/symlink/drv8833.pdf">Datasheet</a> 
<br><br>
<br><br>
Take the motors and put the original hubs and wheels on the shafts. Glue the hub caps to the outside for better looks.
<br><br>
<br><br>
Place motors and bracket on top of the undercarriage and fix the brackets with the tapping screws. Make sure, the outer metal gear plates end up in the small grooves of the undercarriage.
<br><br>
<br><br>
With both motors mounted it should look like this.
<br><br>
<br><br>
Since the steering does not work well with the original wheels, use the printed wheels and place the rubber tires on top of those. 
<br><br>
<br><br>
Use the M3 screws to fix the front wheels to the wheel spindles.
<br><br>
<br><br>
Here it is with all four wheels assembled.
<br><br>
<br><br>
Mount the servo arm to the servo. If you have a servo tester to center the servo first, then the screw can be tightened. Otherwise wait with tightening until the power up test later.
<br><br>
<br><br>
Mounte the servo with arm to the front axle using the tapping screws.
<br><br>
<br><br>
Mount the servo push rod by gently pressing it over the 2 balls of servo arm and steering rack until it snaps in.
<br><br>
<br><br>
This is the wiring diagram including optional LED lights. The pin assignment shown represents the current connections. But they can be completely re-arranged. If so, don't forget to change the channel definitions in <a href="https://github.com/StefansAI/JetCar/blob/main/firmware/jetcar/notebooks/jetcar_car.py">JetCar_Car.py</a>.
<br><br>
<br><br>
The right angle USB cable will be used as power cable.
<br><br>
<br><br>
Cut it at the end of the smaller connector.
<br><br>
<br><br>
Cut the data lines and leave only red (+) and black (-) wires. Solder 3 pairs of extensions for the servo driver board and the 2 H-bridge boards. Use shrink tube to isolate and stabilize the wires.
<br><br>
<br><br>
Plug in the wire connectors from the H-bridges to the servo board, the motor connectors to the H-bridge boards and the USB power cable connectors to all. (This picture does not match the wiring diagram above. It was a first test.)
<br><br>
<br><br>
To prepare the Jetson Nano board, remove the nano module with the heatsink and plug the Wi-Fi-board with the snapped in antennas in. Fix the Wi-Fi card with the original screw.
<br><br>
<br><br>
Snap the nano module back in place.
<br><br>
<br><br>
Mount the fan on top of the heatsink.
<br><br>
<br><br>
Solder the right angle header on the top side of the PiOLED display and plug it into the header connector of the Jetson Nano.
<br><br>
<br><br>
The I2C interface used for this OLED and the servo board is located at the last pins of this connector. Grab some wires and note the colors used at the pins.
<br><br>
<br><br>
Make sure it sits on the correct pins.
<br><br>
<br><br>
Connect to the correct I2C pins on the servo board.
<br><br>
<br><br>
Connect the 2 USB cables to the 2 battery ports and the system should start up for first testing. Make sure to have the micro SD card prepared correctly (see firmware setup) and inserted. The wheels should not touch the ground for this test.
<br><br>
<br><br>
After the Jetson Nano is started up, the OLED display shows the IP address the board is on at this moment. Now open a web browser and type in the top this address plus port number 8888. In this case 192.168.1.105:8888 to connect to the board. Attention: Go through the firmware setup first.
<br><br>
<br><br>
When connected, navigate to the Jupyter notebooks, open and run <a href="https://github.com/StefansAI/JetCar/blob/main/firmware/jetcar/notebooks/JetCar_Basic_Motion.ipynb">JetCar_Basic_Motion.jpynb</a>. You can now move the sliders for steering and throttle. The sliders on top are only indicators, the ones at the bottom for adjustments. 
<br><br>
<br><br>
Adding LEDs to the setup is not necessary, but gives a nice touch. Here is the schematics for the wiring below.<br>
In essence, all back and signal lights are wired as serial pairs without resistor, since there is one on the PWM board for each channel. These LEDs have a forward voltage of around 2V and use small currents. <br>
The white headlights have forward voltages of 3.2V at 20mA and will have to get their own serial resistors. Each pair can now be driven by their individual H-bridge.
<br><br>
<br><br>
For the LED wiring use thinner and more flexible wires to connect between the LEDs and the stiffer ones with the connector just to get to the header. Fix the LEDs and wires with hot glue, which can be peeled off if needed.
<br><br>
<br><br>
The headlight LEDs have all their serial resistors in shrink tubes with the wires coming out to connect to the other side.
<br><br>
<br><br>
The back side is easier. The red wire is +5V connecting all serial pairs on one side. The other side goes directly to the PWM servo board outputs, which already have a serial resistor on board.
<br><br>
<br><br>
Front view with LEDs.
<br><br>
<br><br>
Back view with LEDs.
<br><br>
<br><br>
Now comes the trickiest part of the whole assembly. The LED wires won't have so much room and need to be short. But this makes it really hard to plug in when putting the lower body part on the undercarriage.
<br><br>
<br><br>
Place the body on top, but don't screw it on so it can be moved. Now use tweezers to grab one by one through the top openings and place them on the correct header. Lift or move the body a bit to the sides for better access. It takes a moment to get them all in. Good luck.
<br><br>
<br><br>
Now another test exactly the same way as above with the JetCar_Basic_Motion notebook. This time turn on one by one all LED check boxes to verify them.
<br><br>
<br><br>
Mount the upper body on top and fix with screws.
<br><br>
<br><br>
Plug in USB connectors and place battery in compartment after placing the switch piece into the opening. Sand it down if necessary. In the end it should easily turn on the battery pack with one click and turn off with a double click. The cables are running on the side to the front.
<br><br>
<br><br>
Now place the flatbed with the Jetson Nano on top. It slides under in the front and can be fixed with 2 screws in the back. Connect the power cable and the I2C wires with tweezers.
<br><br>
<br><br>
Screw the camera mount to the cabin and screw in the camera board.
<br><br>
<br><br>
Plug in the flex cable of the camera into the Jetson Nano connector. Lift the plastic part, place the flex board in and press the tiny plastic part back in. Make sure, it is held in and doesn't come out.
<br><br>
<br><br>
Congratulation. It's done and ready to go.
<br><br><br>

- <a href="BOM.md">BOM</a><br>
- <a href="SD%20Card%20Setup.md">SD Card Setup</a><br>

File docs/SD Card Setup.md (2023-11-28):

<h1 style="text-align: center;">JetCar</h1>
<h2 style="text-align: center;">SD Card Setup</h2>
<br><br>
<br><br>
JetCar runs on the <a href="https://developer.nvidia.com/embedded/jetpack">Jetpack</a> image provided by NVIDIA. Several different versions are available for download and there is a lot of other information to find.
<br><br>
<br><br>
The last version with Jetson Nano support can be found under JetPack 4.6.3 in the archive section. But when opening the page, the version for download is actually <a href="https://developer.nvidia.com/jetpack-sdk-463">4.6.1</a>. Open the link and hit the download button.
<br><br>
<br><br>
The preparation is exactly the same as described on this <a href="https://jetbot.org/master/software_setup/sd_card.html">JetBot page</a>, just use the jetpack image instead. Flash the image with the <a href="https://www.balena.io/etcher">Balena Etcher</a>, plug the card into the Jetson Nano, connect monitor, mouse and keyboard and boot the system.
<br><br>
<br><br>
After initial startup, go through the standard setup dialogs. As in the JetBot setup, the user and password can be simplified to just jetson for everything if JetCar operates later inside a sandbox network.
<br><br>
<br><br>
For all startup initialization the Jetson Nano has to have a wired or wireless internet connection, which can be later replaced by a separate Wi-Fi.
<br><br>
<br><br>
Open the browser and open github.com/StefansAI/JetCar/firmware and click on the file <a href="https://github.com/StefansAI/JetCar/blob/main/firmware/install.sh">"install.sh"</a>. Once open, click on the RAW button in the upper right.
<br><br>
<br><br>
Then go up the File menu and hit "Save page as.."
<br><br>
<br><br>
The dialog changed the extension to .txt, make sure to rename it back to .sh and save in the Home directory. Hit the save button in the lower right.
<br><br>
<br><br>
Open the terminal and type:<br>

```
chmod +x install.sh
./install.sh [root_password]
```

The script will run now for about an hour to install everything needed.
<br>
At this point, the JetCar can be cut off from the internet by switching Wi-Fi settings to a sandbox Wi-Fi. It will be best to use a separate Wi-Fi router only connected to the PC to connect the JetCar to. This way, the JetCar will not have to share all the Wi-Fi traffic of the family watching Netflix, YouTube or Prime :-)
<br><br>
<br><br>
After the installation, the PiOLED display should show an IP address. Open a browser on the PC and type that address in plus port number 8888. For instance in this case it would be 192.168.1.103:8888.
<br><br>
<br><br>
The log-in for Jupyter will be the same as the user log in on the Jetson Nano. 
<br><br>
<br><br>
Jupyter comes up in the home directory. Navigate to JetCar/notebooks.  
<br><br>
<br><br>
It is easier to download the firmware subfolder to your local PC and then simply select all files in the File Explorer to drag them over to the web browser with Jupyter open at JetCar/notebooks/. 
<br><br>
<br><br>
Have a look at the different files in this folder. There are 3 Jupyter notebooks and several Python files. The first notebook needed, is the JetCar_Basic_Motion for testing the assembly.
<br><br>
Since from now on, all communications with the JetCar can go through Jupyter, the graphic user interface can be removed to save resources:
<a href="https://lunar.computer/posts/nvidia-jetson-nano-headless/">Jetson Nano Headless</a><br>
<br><br>
In the end it might be also good to apply "sudo apt-get autoremove" and "sudo apt-get clean" from the Jupyter terminal for instance.
<br><br><br>

- <a href="BOM.md">BOM</a><br>
- <a href="Assembly.md">Assembly</a><br>
- <a href="Data%20Preparation.md">Data Preparation with ImageSegmenter</a><br>

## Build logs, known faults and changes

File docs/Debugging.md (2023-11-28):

<h1 style="text-align: center;">JetCar</h1>
<h2 style="text-align: center;">Debugging</h2>
<br><br>
Debugging a real-time system is a special task. The GUI cannot give all the information needed to recognize an issue and it also might disappear very quickly. It is not possible to step through the code in real-time. The printf-commands can be very intrusive to the real-time performance and should be avoided.<br>
What works well for real-time embedded systems is logging. If possible, log binary information in RAM to be stored and processed later. But here it was best to simply store the camera frame and the mask from the inference to the SD card. The system normally buffers in RAM and writes to SD in the background.<br>
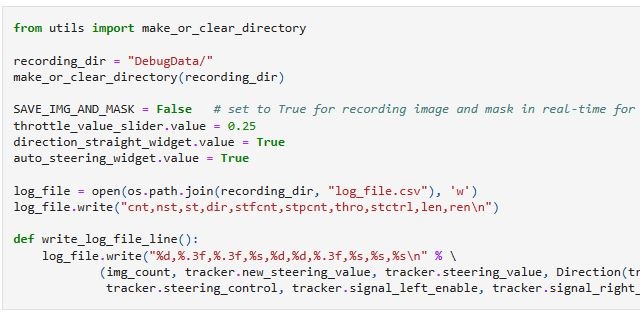
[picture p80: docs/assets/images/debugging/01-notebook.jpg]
<br>
For this reason, the Jupyter notebook <a href="https://github.com/StefansAI/JetCar/blob/main/firmware/jetcar/notebooks/JetCar_Auto_Drive.ipynb">JetCar_Auto_Drive.jpynb</a> has this cell above. If there is any wrong behavior, set SAVE_IMG_AND_MASK to true:<br>

```Python
recording_dir = "DebugData/"
make_or_clear_directory(recording_dir)

SAVE_IMG_AND_MASK = True   # set to True for recording image and mask in real-time for offline debugging
```

This enables these lines in the execute function:<br>

```Python
 # If enabled, save image frame and mask 
    if SAVE_IMG_AND_MASK == True:
        save_img_and_mask(recording_dir, img_count, image, mask)
```
With this, repeat the same scenario and let it record images and masks in the recording_dir. Just record enough to include the issue and then stop.
<br><br>
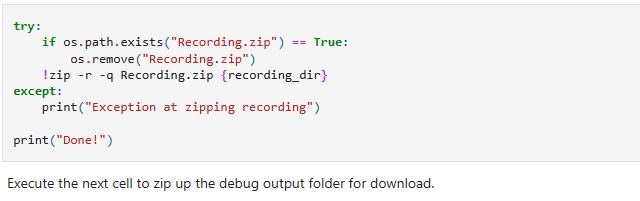
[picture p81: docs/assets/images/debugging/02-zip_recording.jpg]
<br>
Execute this cell after stopping and download the file "Recording.zip".<br><br>
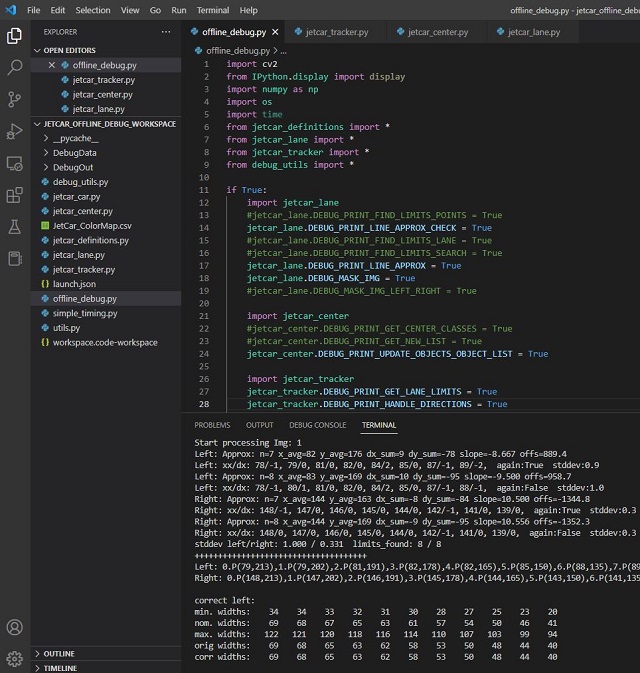
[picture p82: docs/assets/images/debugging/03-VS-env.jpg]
<br>
Set up an environment with <a href="https://code.visualstudio.com/Download">Visual Code</a> for instance and copy the <a href="https://github.com/StefansAI/JetCar/tree/main/firmware/offline_debug">offline debug files</a> and all needed Python files from <a href="https://github.com/StefansAI/JetCar/tree/main/firmware/jetcar/notebooks">JetCar/notebooks/</a><br>:

- <a href="https://github.com/StefansAI/JetCar/tree/main/firmware/jetcar/notebooks/jetcar_definitions.py">jetcar_definitions.py</a>
- <a href="https://github.com/StefansAI/JetCar/tree/main/firmware/jetcar/notebooks/jetcar_tracker.py">jetcar_tracker.py</a>
- <a href="https://github.com/StefansAI/JetCar/tree/main/firmware/jetcar/notebooks/jetcar_center.py">jetcar_center.py</a>
- <a href="https://github.com/StefansAI/JetCar/tree/main/firmware/jetcar/notebooks/jetcar_lane.py">jetcar_lane.py</a>

Open <a href="https://github.com/StefansAI/JetCar/blob/main/firmware/offline_debug/offline_debug.py">offline_debug.py</a>. At the top it defines the input and output directories and the range of image/mask pairs to be processed:<br>

```Python
RECORDING_MIN = 0 
RECORDING_MAX = 1000
RECORDING_DIR = "DebugData/"
MASK_OUTPUT_DIR = "DebugOut/"
```

In the python files from the JetCar all debug outputs are disabled for faster runtime. But here you can selectively enable anything of interest by just commenting or uncommenting any line:<br>

```Python
if True:
    import jetcar_lane
    #jetcar_lane.DEBUG_PRINT_FIND_LIMITS_POINTS = True
    jetcar_lane.DEBUG_PRINT_LINE_APPROX_CHECK = True
    #jetcar_lane.DEBUG_PRINT_FIND_LIMITS_LANE = True
    #jetcar_lane.DEBUG_PRINT_FIND_LIMITS_SEARCH = True
    jetcar_lane.DEBUG_PRINT_LINE_APPROX = True
    jetcar_lane.DEBUG_MASK_IMG = True
    #jetcar_lane.DEBUG_MASK_IMG_LEFT_RIGHT = True

    import jetcar_center
    #jetcar_center.DEBUG_PRINT_GET_CENTER_CLASSES = True
    #jetcar_center.DEBUG_PRINT_GET_NEW_LIST = True
    jetcar_center.DEBUG_PRINT_UPDATE_OBJECTS_OBJECT_LIST = True

    import jetcar_tracker
    jetcar_tracker.DEBUG_PRINT_GET_LANE_LIMITS = True
    jetcar_tracker.DEBUG_PRINT_HANDLE_DIRECTIONS = True
    jetcar_tracker.DEBUG_PRINT_PROCESS_CLASSES = True
```
<br>
After those definitions it loads these 2 files, that have to be available. One is the color map that matches the one from the JetCar. And the other one contains log entries from the run. The next direction requests, stored here, will be loaded with each frame below to synch up the recording run with the debug run.

```Python
color_map = load_color_map("jetcar_colormap.csv")
log_file = load_log_file(os.path.join(RECORDING_DIR, "log_file.csv"))
```

<br>
The main loop can be boiled down to just reading the files and process the mask and direction.<br>:

```Python
for img_count in range(RECORDING_MIN,RECORDING_MAX):
    print("Start processing %s" %("Img: %d" %(img_count)))
    filename = 'Img_%03d.jpg' % (img_count)
    image_path = os.path.join(RECORDING_DIR, filename)
    
    if os.path.exists(image_path):
        image = cv2.imread(image_path)
     
        filename = 'Mask_%03d.npy' % (img_count)
        mask_path = os.path.join(RECORDING_DIR, filename)
        mask = np.load(mask_path,mmap_mode='r') 
        #...
        if img_count < len(log_file.index):
            next_direction = Direction[log_file.loc[img_count]['nextdir']]
        #...
        if img_count > 0:
            tracker.process(mask, next_direction)
        
        print("Img: %d ->processed!" %(img_count))
  
    else:
        break

```

Constants in Python are actually variables and can be changed at runtime and here it can be used as a benefit. You can change the direction at a specific frame number or turn on more logging at another frame number to dig into the code.<br>
The next direction requests loaded from the log file can also be overwritten here if needed.
<br>

```Python
        if img_count == 0:
            next_direction = Direction.Straight
        if img_count == 10:
            next_direction = Direction.Right
        #if img_count == 40:
        #    next_direction = Direction.Left
        elif img_count == 22:
            jetcar_tracker.DEBUG_PRINT_GET_LANE_LIMITS = True
            jetcar_lane.DEBUG_MASK_IMG_LEFT_RIGHT = True
            jetcar_lane.DEBUG_PRINT_LINE_APPROX_CHECK = True
            jetcar_lane.DEBUG_PRINT_FIND_LIMITS_LANE = True
            jetcar_lane.DEBUG_PRINT_FIND_LIMITS_POINTS = True
            jetcar_center.DEBUG_PRINT_GET_CENTER_CLASSES = True
        elif img_count == 23:
            break

```

Besides utilizing all the possible logging capabilities, you can now also step through the code. And you can break at a specific frame and then step through.
<br><br>
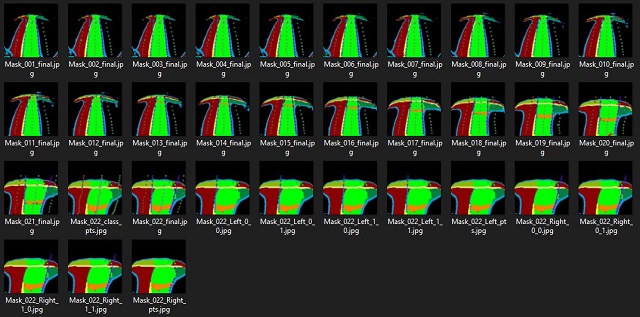
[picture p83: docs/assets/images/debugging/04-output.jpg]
<br>
The output directory now contains readably mask images with overlaid information and more outputs for frame 22.<br><br>
The Terminal window contains all the logging output for each frame. It could look like this for instance:<br>

```
Start processing Img: 21
Left: Approx: n=7 x_avg=84 y_avg=176 dx_sum=4 dy_sum=-78 slope=-19.500 offs=1822.6
Left: xx/dx: 83/1, 83/1, 84/2, 84/-6, 85/0, 86/2, 87/1, 87/-4,  again:True  stddev:2.4
Left: Approx: n=8 x_avg=85 y_avg=169 dx_sum=5 dy_sum=-95 slope=-19.000 offs=1779.2
Left: xx/dx: 82/0, 83/1, 84/2, 84/-6, 85/0, 86/2, 87/1, 87/0,  again:False  stddev:2.4
Right: Approx: n=7 x_avg=163 y_avg=176 dx_sum=25 dy_sum=-78 slope=-3.120 offs=685.7
Right: xx/dx: 152/0, 155/1, 159/2, 163/2, 167/0, 172/-3, 177/0, 182/1,  again:True  stddev:1.5
Right: Approx: n=8 x_avg=166 y_avg=169 dx_sum=30 dy_sum=-95 slope=-3.167 offs=693.5
Right: xx/dx: 152/0, 155/1, 159/2, 163/2, 167/0, 172/-3, 176/-1, 182/0,  again:False  stddev:1.5
stddev left/right: 2.398 / 1.536  limits_found: 8 / 8
+++++++++++++++++++++++++++++++++++++
Left: 0.P(82,213),1.P(82,202),2.P(82,191),3.P(90,178),4.P(85,165),5.P(84,150),6.P(86,135),7.P(87,118),8.P(88,101),9.P(89,82),10.P(90,63),
Right: 0.P(152,213),1.P(154,202),2.P(157,191),3.P(161,178),4.P(167,165),5.P(175,150),6.P(177,135),7.P(182,118),8.P(187,101),9.P(193,82),10.P(199,63),

min. widths:    35    34    33    34    32    30    28    26    24    22    20
nom. widths:    70    69    67    68    64    61    57    53    49    45    40
max. widths:   123   122   120   121   117   114   110   106   102    98    93
orig widths:    70    72    75    71    82    91    91    95    99   104   109
corr widths:    70    72    75    71    82    91    91    95    99   104   109

Left: 0.P(82,213),1.P(82,202),2.P(82,191),3.P(90,178),4.P(85,165),5.P(84,150),6.P(86,135),7.P(87,118),8.P(88,101),9.P(89,82),10.P(90,63),
Right: 0.P(152,213),1.P(154,202),2.P(157,191),3.P(161,178),4.P(167,165),5.P(175,150),6.P(177,135),7.P(182,118),8.P(187,101),9.P(193,82),10.P(199,63),
+++++++++++++++++++++++++++++++++++++
get_lane_limits done: left=-19.0 right==-3.2 slope_avg=-11.1
Left objects: -31:143:lane_wrong_dir:20:3  124:10:yellow_dashed_line:0:3  134:19:lane_left_turn:1:3  135:9:yellow_dashed_line:6:1  144:10:lane_left_turn:8:1  153:9:nothing:1:3  154:9:white_shoulder_line:2:1  164:4:nothing:4:1
Center objects: 47:7:lane_right_turn:0:3  53:6:yield_line:10:3  124:10:yellow_dashed_line:8:3  152:9:white_shoulder_line:1:2  153:9:nothing:3:3
Right objects: -83:162:nothing:20:3  81:13:white_shoulder_line:5:3  90:26:lane_right_turn:6:3  116:8:yellow_dashed_line:5:3  125:10:lane_wrong_dir:5:3  135:28:nothing:1:3  151:9:nothing:5:1
process_classes direction:Straight  next_turn_direction:Right  stop_count=0
i:1 code: 8=yield_line in INTERSECTION_OBJECT_CODES
update_throttle  brake_light_enable=True, throttle_new_value=0.750, throttle_value=0.781
process_classes done, intersection=True, allowed:left=True, straight=True, right=True slope_avg=-11.1
current direction(Straight) != next_turn_direction(Right)
steering value:0.209  dir:Straight
Img: 21 ->processed!
```

A log with all debug outputs turned on is just too much information to go through. It is best to leave all DEBUG_PRINT_... constants off and only enable the specific ones that are relevant for the current debugging goal.<br>
It is very likely, that problems occur in the top level where all the decisions are made. This happens in these two methods of the LaneTracker class  in <a href="https://github.com/StefansAI/JetCar/tree/main/firmware/jetcar/notebooks/jetcar_tracker.py">jetcar_tracker.py</a>:
<br>

```Python
    def process_classes(self, next_turn_direction: Direction):
        """ Processes the objects in the center of the current lane and handles 
        direction arrow street markings to determine the allowed directions of 
        any intersection, the slow down and brake lights when entering an intersection
        or acceleration when the intersection is passed.
        next_turn_direction     -- direction code for the next upcoming turn.  """

```
<br>

```Python
    def handle_directions(self, mask, next_turn_direction: Direction):
        """ Check for direction change request and look for left or right lane codes 
        and initiate the turn when recognized. In case of no turn, a steering value is 
        calculated to keep the car in the center of the current lane.
        mask                -- segmentation mask containing the SegmClass code.
        next_turn_direction -- direction code for the next upcoming turn. """
```

Many decisions are made using the constant definition at the top of <a href="https://github.com/StefansAI/JetCar/tree/main/firmware/jetcar/notebooks/jetcar_tracker.py">jetcar_tracker.py</a>. Before changing the code, it might help to change these constants:<br>

```Python
# When less points are found, run corrections on the points
LIMIT_FOUND_CORRECTION_THRESHOLD = N_SEARCH_POINTS - 2
# Few y coordinates for calculating the steering value
STEERING_Y = [IMG_YMAX, (IMG_YMAX+IMG_YC)//2, IMG_YC]
# Scaling factor from x coordinate to steering value
STEERING_X_SCALE = 2.5*IMG_XC
# Number of cycles to stop at the wait line
THROTTLE_STOP_CYCLES = 10
# Throttle value when approaching an intersection
THROTTLE_VALUE_APPROACHING_INTERSECTION = 0.75
# Throttle value when entering the inner intersection area
THROTTLE_VALUE_ENTERING_INTERSECTION = 0.6
# Throttle value to be used in a turn of an intersection
THROTTLE_VALUE_IN_TURN = 0.8
# Throttle value to be used in a curve outside intersections
THROTTLE_VALUE_IN_CURVE = 0.9
# Steering value threshold for reducing the speed to THROTTLE_VALUE_IN_CURVE
THROTTLE_CURVE_STEERING_THRESHOLD = 0.3
# Filter coefficient to low pass new throttle value with old one
THROTTLE_VALUE_FILTER_COEFF = 0.25
# Number of cycles to keep the current steering value when turning
STEERING_FIXED_TURN_CYCLES = 16
# Cycle count in fixed turn to switch to diagonal search
STEERING_FIXED_TURN_DIAG_CYCLES = (STEERING_FIXED_TURN_CYCLES//2) + 2
# Fixed steering value used for left turn, left turn can be wider
STEERING_LEFT_TURN_VALUE = -0.8
# Fixed steering value used for right turn, right turn must be tight
STEERING_RIGHT_TURN_VALUE = 1.0
# Minimum distance of left turn code to ORIGIN to start turning left
MIN_TURN_LEFT_DISTANCE = 100
# Minimum distance of right turn code to ORIGIN to start turning right
MIN_TURN_RIGHT_DISTANCE = 60
# Minimum limit found point count to check for switching back to straight after turn
MINIMUM_LIMIT_FOUND_POINTS = (2*N_SEARCH_POINTS)//3
# A threshold to smooth out small steering changes with a low pass
STEERING_FILTER_THRESHOLD = 0.05
# An average slope threshold for intersection detection to see if there is "Nothing" ahead
AVG_SLOPE_THRESHOLD_INTERSECTION = 5
# Switch back to straight direction when new average slope value goes above after turn
AVG_SLOPE_THRESHOLD_STRAIGHT = 3
# Switch to diagonal direction when new verage slope falls below
AVG_SLOPE_THRESHOLD_DIAG = 0.9
```
<br><br><br>

- <a href="Operation.md">Operation</a><br>
- <a href="../README.md">Read Me</a><br>

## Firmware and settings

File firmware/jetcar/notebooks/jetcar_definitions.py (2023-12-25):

# SPDX-FileCopyrightText: 2021 Stefan Warnke
#
# SPDX-License-Identifier: BeerWare

"""
`jetcar_definitions`
====================
Main definitions for the jetcar code. 
Besides image size, this file contains segmentation class definitions and
grouping lists of these segmentaion classes used in the code:

class SegmClass(enum.Enum):
    Definition of all segmentation class names and values

class Side(enum.Enum):
    Definitions of a side from the current lane

class Direction(enum.Enum):
    Definitions of simplified driving directions 
    

* Author(s): Stefan Warnke

Dependencies:
-
"""

import enum

# Image size in both dimensions x and y
IMG_SIZE = 224 

# Center x and y coordinates in the image or mask
IMG_XC = IMG_SIZE//2
IMG_YC = IMG_SIZE//2

# Maximum indices in x and y dimensions
IMG_XMAX = IMG_SIZE-1
IMG_YMAX = IMG_SIZE-1

# Scene Parsing has N classes including nothing=0
N_CLASSES = 19

# Definition of all segmentation class names and values
class SegmClass(enum.Enum):
    nothing = 0
    white_shoulder_line = 1
    yellow_solid_line = 2
    yellow_dashed_line = 3
    yellow_double_line = 4
    lane_driving_dir = 5
    lane_wrong_dir = 6
    lane_left_turn = 7
    lane_right_turn = 8
    yield_line = 9
    stop_line = 10
    stop_text = 11
    arrow_straight = 12
    arrow_straight_left = 13
    arrow_straight_right = 14
    arrow_left_only = 15
    arrow_right_only = 16
    arrow_left_right = 17
    parking_sign = 18
    #Unused:
    white_solid_line = 100
    white_dashed_line = 101
    white_double_line = 102
    yellow_solid_dashed_line = 103
    yellow_dashed_solid_line = 104
    lane_limit_line = 105
    lane_center = 106
    yield_text = 107
    crosswalk_lines = 108
    crosswalk_zebra = 109
    merge_left = 110
    merge_right = 111

# Declare some special codes used directly in the classes
NOTHING_CODE =  SegmClass.nothing.value
LANE_MY_DRIVING_DIR_CODE = SegmClass.lane_driving_dir.value
LANE_LEFT_TURN_CODE = SegmClass.lane_left_turn.value
LANE_RIGHT_TURN_CODE = SegmClass.lane_right_turn.value
STOP_LINE_CODE = SegmClass.stop_line.value
STOP_TEXT_CODE = SegmClass.stop_text.value

# Code list definition for unspecified background
NOTHING_CODES = [NOTHING_CODE]

# Code list definition for my own lane only
MY_LANE_ONLY_CODES = [  
    LANE_MY_DRIVING_DIR_CODE]
 
# Code list definition for my own lane and left turn lane
MY_LANE_AND_LEFT_TURN_CODES = [  
    LANE_MY_DRIVING_DIR_CODE,
    LANE_LEFT_TURN_CODE]
 
# Code list definition for my own lane and right turn lane
MY_LANE_AND_RIGHT_TURN_CODES = [  
    LANE_MY_DRIVING_DIR_CODE,
    LANE_RIGHT_TURN_CODE]

# Code list definition for all of my lanes 
MY_LANE_CODES = [  
    LANE_MY_DRIVING_DIR_CODE, 
    LANE_LEFT_TURN_CODE, 
    LANE_RIGHT_TURN_CODE]

# Code definitions identifying blocking the straight ahead direction
STRAIGHT_BLOCK_CODES = [
    NOTHING_CODE, 
    SegmClass.lane_wrong_dir.value
]

# Code list definition for all possible lane limits on 
# the left side of the lane straight ahead
STRAIGHT_LANE_LIMIT_CODES_LEFT = [ 
    NOTHING_CODE, \
    SegmClass.white_shoulder_line.value, \
    SegmClass.white_solid_line.value, \
    SegmClass.white_dashed_line.value, \
    SegmClass.white_double_line.value, \
    SegmClass.yellow_solid_line.value, \
    SegmClass.yellow_dashed_line.value, \
    SegmClass.yellow_double_line.value, \
    SegmClass.lane_wrong_dir.value, \
    SegmClass.lane_left_turn.value, \
    SegmClass.lane_right_turn.value]

# Code list definition for all possible lane limits on 
# the right side of the lane straight ahead
STRAIGHT_LANE_LIMIT_CODES_RIGHT = [ 
    NOTHING_CODE, \
    SegmClass.white_shoulder_line.value, \
    SegmClass.white_solid_line.value, \
    SegmClass.white_dashed_line.value, \
    SegmClass.white_double_line.value, \
    SegmClass.yellow_solid_line.value, \
    SegmClass.yellow_dashed_line.value, \
    SegmClass.yellow_double_line.value, \
    SegmClass.lane_wrong_dir.value, \
    SegmClass.lane_right_turn.value]

# Code list definition for all possible lane limits on 
# the left side of the left turn direction
LEFT_TURN_LIMIT_CODES_LEFT = [ 
    SegmClass.white_shoulder_line.value, \
    SegmClass.white_solid_line.value, \
    SegmClass.white_dashed_line.value, \
    SegmClass.white_double_line.value, \
    SegmClass.yellow_solid_line.value, \
    SegmClass.yellow_dashed_line.value, \
    SegmClass.yellow_double_line.value, \
    SegmClass.lane_wrong_dir.value]

# Code list definition for all possible lane limits on 
# the right side of the left turn direction
LEFT_TURN_LIMIT_CODES_RIGHT = LEFT_TURN_LIMIT_CODES_LEFT

# Code list definition for all possible lane limits on 
# the left side of the right turn direction
RIGHT_TURN_LIMIT_CODES_LEFT = LEFT_TURN_LIMIT_CODES_LEFT

# Code list definition for all possible lane limits on 
# the right side of the right turn direction
RIGHT_TURN_LIMIT_CODES_RIGHT = LEFT_TURN_LIMIT_CODES_LEFT
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

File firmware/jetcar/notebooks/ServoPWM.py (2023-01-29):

# SPDX-FileCopyrightText: 2021 Stefan Warnke
#
# SPDX-License-Identifier: BeerWare

"""
`ServoPWM`
==========

Adding PWM channels to Servo implementations in adafruit_servokit.
The PCA9685 chip is naturally a PWM chip. adafruit_servokit reduces the
PWM range to realize servo timing. This module introduces the PWM
range mapped from 0.0 to 1.0 in parallel to servo functionality.

* Author(s): Stefan Warnke

Dependency:
Adafruit's Servo Kit library: https://github.com/adafruit/Adafruit_CircuitPython_ServoKit.git
"""
from adafruit_servokit import ServoKit

__version__ = "0.0.0-auto.0"
__repo__ = "https://github.com/..."


class PWM:
    """ PWM channel class similar to the adafruit servo classes.
    This class maps the range 0.0 to 1.0 to the PWM range of the chip.
    For more flexibility the maximum duty cycle can be reduced.

    :param pwm_out: Reference to PCA9685 channel object to be linked to.
    """
    def __init__(self, pwm_out):
        self._pwm_out = pwm_out
        self._max_duty = 0xFFFF
    
    @property
    def fraction(self):
        """Pulse width expressed as fraction between 0.0 and 1.0 (`max_duty`)."""
        if self._pwm_out.duty_cycle == 0:  
            return 0
        return self._pwm_out.duty_cycle / self._max_duty

    @fraction.setter
    def fraction(self, value):
        if value <= 0:
            self._pwm_out.duty_cycle = 0  
        elif value >= 1.0:
            self._pwm_out.duty_cycle = self._max_duty 
        else:
            self._pwm_out.duty_cycle = int(value * self._max_duty)
            
    @property
    def max_duty(self):
        """Maximum PWM duty cycle, normally 0xFFFF, but can be reduced to a lower required level"""
        return self._max_duty
    
    @max_duty.setter
    def max_duty(self, value):
        if value <= 1:
            self._max_duty = 1  
        elif value >= 0xFFFF:
            self._max_duty = 0xFFFF
        else:
            self._max_duty = int(value)

 
class _PWM:
    """This class creates the array access to the list of PWM objects."""
    def __init__(self, kit):
        self.kit = kit

    def __getitem__(self, pwm_channel):
        num_channels = self.kit._channels
        if pwm_channel >= num_channels or pwm_channel < 0:
            raise ValueError("servo must be 0-{}!".format(num_channels - 1))
        pwm = self.kit._items[pwm_channel]
        if pwm is None:
            pwm = PWM(self.kit._pca.channels[pwm_channel])
            self.kit._items[pwm_channel] = pwm
            return pwm
        if isinstance(self.kit._items[pwm_channel], PWM):
            return pwm
        raise ValueError("Channel {} is already in use.".format(pwm_channel))

    def __len__(self):
        return len(self.kit._items)

    
class ServoPWM(ServoKit):
    """ServoPWM inherits everything from Adafruit's ServoKit and adds the pwm objects in parallel to servo and continues_servo"""
    def __init__(self,*,channels=16,i2c=None,address=0x40,reference_clock_speed=25000000,frequency=50):
        super().__init__(channels=16,i2c=None,address=0x40,reference_clock_speed=25000000,frequency=50)
        self._pwm=_PWM(self)
            
    @property
    def pwm(self):
        """Accesses the list of PWM objects."""
        return self._pwm
          

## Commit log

2022-01-12 Add files via upload
    A sample dataset with a few images.
2023-01-29 Check in all current state of Jan 2023
    [Battery.step, Camera Mount Top.step, Camera Mount Top.stl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]
2023-10-10 Print update
2024-01-10 Update BOM.md
    Correction
2024-01-10 Update BOM.md
    Camera link correction
2024-02-25 Increase stand-off diameter to avoid breaking
    the stand-off diameter is increased from 5mm to 7mm
    [Flatbed-JetsonNano.step, Flatbed-JetsonNano.stl]
